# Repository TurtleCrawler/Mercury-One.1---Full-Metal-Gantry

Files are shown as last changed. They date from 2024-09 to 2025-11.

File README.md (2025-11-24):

# Mercury One.1 - Full Metal Gantry

___

 These are a self source design using laser cut aluminum plates from vendors like SendCutSend. The entire belt path and gantry has been moved lower than the stock printed parts. You cannot mix and match these parts with stock printed stepper mounts, xjoints, or front towers. If you already have my metal stepper mounts, you can still use the same metal plates and upgrade to the full metal gantry.

**Assembly steps will be added later, for now you will have to reference the CAD.**
___

**Imperial files:**

- Mainly for those sourcing material in North America
- Files are designed 1/8 inch thick plate (.125in or 3.175mm)

**Metric files:**

- Files are designed for 3mm thick plate (.118in)
- You will also need to use M5 washers under the M5 bolts in the stepper towers to prevent the bolts from bottoming out on the extrusion.

**Other Notes:**

- Top Mount for toolheads designed around the stock Zerog Mercury one.1 belt path.
- Front Mount for any toolhead made for a front mounted MGN12 rail.
- Stepper Tower printed insert pairs should measure slightly less than the height of the aluminum spacers used. If your pairs are 0.2-0.4mm short, you can use the offset files to reduce the gap.
- 9mm Xjoints are designed for a live idler setup, which will require modifying a 20t pulley by removing the hub.
- Youtube Video on pulling the Hub <https://youtu.be/RKpxDKYOJYs?si=vfwZNFjSuAocWLpN>

**Tools Needed:**

- Drill press
- 90 degree Countersinking bit (82 degree also works)
- 220 grit sandpaper (For sanding dowel pins to fit into the bearings)
- Cordless drill (Use with a spare dowel pin to ream the dowel pin holes to size as needed)

___

## 9mm Full Metal Gantry With Live Idler

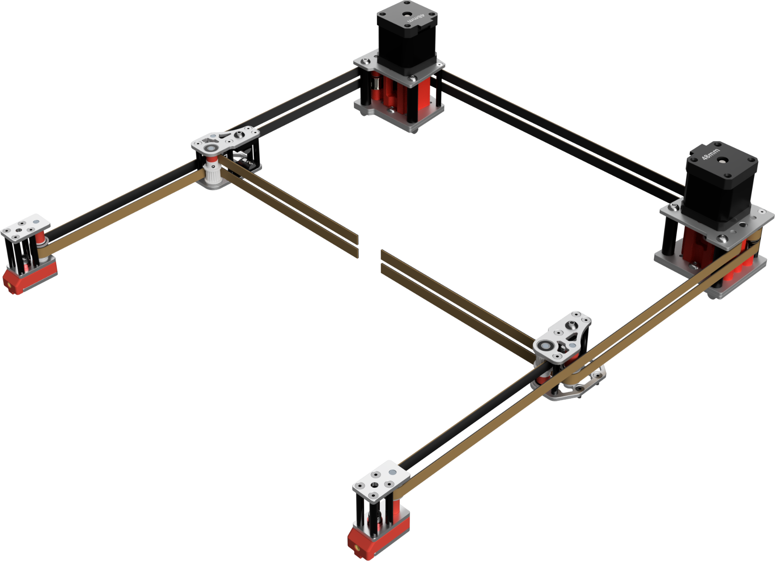
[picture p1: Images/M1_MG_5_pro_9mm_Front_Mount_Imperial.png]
 

___

## 6mm Full Metal Gantry

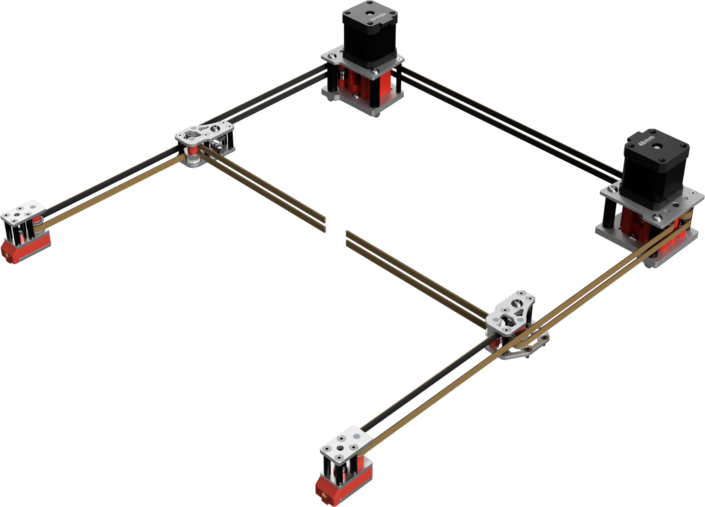
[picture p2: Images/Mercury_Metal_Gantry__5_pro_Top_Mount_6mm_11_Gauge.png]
Metal Stepper Towers
  

___

## Sourcing

Laser cutting services:

- Sendcutsend <https://sendcutsend.com/>
- Laserboost <https://www.laserboost.com/>

Aluminum Spacers and Standoffs:

- D5xM3 Length 10mm <https://www.aliexpress.us/item/3256805776299657.html>
- M5 Length 3mm or 4mm <https://www.aliexpress.us/item/3256802832337103.html>
- 5mmx8mm 35/40mm Spacers <https://www.aliexpress.us/item/3256805365722139.html>
- M3 Threaded spacers <https://www.aliexpress.us/item/2251832625574286.html>
- 5x26mm Dowel Pins <https://www.aliexpress.us/item/3256803593912582.html>
- 5x36mm 5x26mm Dowel Pins <https://www.aliexpress.us/item/2251832864425146.html>
- M5 shims <https://www.aliexpress.us/item/3256801130894631.html>

___

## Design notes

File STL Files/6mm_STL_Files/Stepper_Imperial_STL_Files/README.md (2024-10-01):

# Mercury One.1 - Full Metal Gantry

## 6mm Imperial Stepper Mount Files

These are the files for 6mm belts using Imperial 1/8in thick plates (.125in or 3.175mm) If your plates are 3mm (.118in) then please use the Metric files.

## Offset Files

The offset files have an extra 0.2mm added to the bottom faces. This is due to some printers loosing up to 1 layer height in the start of the prints. First print the standard files, and measure the stack height for the left and right sets. They should add up to 34.81mm to 35mm. If they come in 0.2mm short, you can reprint either the tops or bottoms. And if they are 0.4mm short, then print all of the files needed from the offset files. (A gap of 0.2mm to 0.4mm is also mainly just cosmetic, so you can also skip reprinting if the gap does not bother you.)

## Double Shear Bearing Support Files

5mm shafts without being supported on the other end of the pulley, limit your belt tension to around 110hz. Going past this could bend your stepper shafts. I have included files to support a handful of bearings for a double shear setup. You will need stepper motors with longer stepper shafts than normal, 40 or longer. See the chart bellow for supported bearings.

### Motor and Bearing supports

- Kraken motors (40x5mm Shafts) should work with 625-2RS (5x16x5mm) and 635-RS (5x19x6mm) bearings.
- 55x5mm Shafts will work with 625-RS (5x16x5mm) and 635-2RS (5x19x6mm) bearings.
- 55x8mm Shafts will work with 698-RS (8x19x6mm) and F608-2RS (8x22x7mm) bearings.

### Bearing Notes

- F in front of a bearing name denotes that it is a flanged bearing
- 2RS on the end of a bearing part number means it has 2 Rubber Seals
- RS calls for one rubber seal, and one open side. Though often stores like Amazon will list their 2RS bearings using just RS.
- ZZ on the end of a bearing part number means it uses 2 metal shields in place of seals.
- You will most likely need to sand the ends of your stepper shafts to fit the bearing bores.
- F608-2RS note: I recommend using green bearing retaining compound on the outside fo the bearing, as the 22mm holes in the laser cut plates are not a press fit.

___

Flange stacks are same as the stock Mercury one.1, all shims are M5x1 and placed as shown in the image below.

Stepper Mount Bearing Stacks

Countersink the holes marked in red. Marking them in advanced with a sharpie can help prevent countersinking the wrong holes. You only need to countersink 4 of the 6 plates.

Stepper Mount Countersink Holes

___

## DXF Plate BOM

| Part Description | Quantity |
|---|---|
| Stepper Top-Center Plate_x4.dxf | 4 |
| Stepper Bottom Plate_x2.dxf | 2 |

## 6mm Imperial Stepper Mount Hardware BOM

| Part Description | Quantity |
|---|---|
| M3x30 standoffs | 8 |
| M5x30 Spacer (8 or 10mm OD) | 4 |
| 5x40mm Dowel Pins | 4 |
| *F695RS Bearing | 12 |
| *6mm 20t 5mm Bore GT2 Pulley | 2 |
| M3x10 FHCS | 12 |
| M3x12 FHCS | 12 |
| M5x12 BHCS | 2 |
| M5x50 BHCS | 4 |
| M3x4x5mm Heatsets (5mm OD) | 12 |
| M5x1 Shim | 16 |
| **M5x0.1 Shim | 8 |

*Included in default Mercury One.1 BOM

**Optional parts

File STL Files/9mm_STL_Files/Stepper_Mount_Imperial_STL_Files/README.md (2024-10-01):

# Mercury One.1 - Full Metal Gantry

## 9mm Imperial Stepper Mount Files

These are the files for 9mm belts using Imperial 1/8in thick plates (.125in or 3.175mm) If your plates are 3mm (.118in) then please use the Metric files.

## Offset Files

The offset files have an extra 0.2mm added to the bottom faces. This is due to some printers loosing up to 1 layer height in the start of the prints. First print the standard files, and measure the stack height for the left and right sets. They should add up to 34.81mm to 35mm. If they come in 0.2mm short, you can reprint either the tops or bottoms. And if they are 0.4mm short, then print all of the files needed from the offset files. (A gap of 0.2mm to 0.4mm is also mainly just cosmetic, so you can also skip reprinting if the gap does not bother you.)

## Double Shear Bearing Support Files

5mm shafts without being supported on the other end of the pulley, limit your belt tension to around 110hz. Going past this could bend your stepper shafts. I have included files to support a handful of bearings for a double shear setup. You will need stepper motors with longer stepper shafts than normal, 40 or longer. See the chart bellow for supported bearings.

### Motor and Bearing supports

- Kraken motors (40x5mm Shafts) should work with 625-2RS (5x16x5mm) and 635-RS (5x19x6mm) bearings.
- 55x5mm Shafts will work with 625-RS (5x16x5mm) and 635-2RS (5x19x6mm) bearings.
- 55x8mm Shafts will work with 698-RS (8x19x6mm) and F608-2RS (8x22x7mm) bearings.

### Bearing Notes

- F in front of a bearing name denotes that it is a flanged bearing
- 2RS on the end of a bearing part number means it has 2 Rubber Seals
- RS calls for one rubber seal, and one open side. Though often stores like Amazon will list their 2RS bearings using just RS.
- ZZ on the end of a bearing part number means it uses 2 metal shields in place of seals.
- You will most likely need to sand the ends of your stepper shafts to fit the bearing bores.
- F608-2RS note: I recommend using green bearing retaining compound on the outside fo the bearing, as the 22mm holes in the laser cut plates are not a press fit.

___

Flange stacks Use M5x1 shims, refer to the image below for placement.

Stepper Mount Bearing Stacks

Countersink the holes marked in red. Marking them in advanced with a sharpie can help prevent countersinking the wrong holes. You only need to countersink 4 of the 6 plates.

Stepper Mount Countersink Holes

___

## DXF Plate BOM

| Part Description | Quantity |
|---|---|
| Stepper Top-Center Plate_x4.dxf | 4 |
| Stepper Bottom Plate_x2.dxf | 2 |

## 9mm Imperial Stepper Mount Hardware BOM

| Part Description | Quantity |
|---|---|
| M3x40 standoffs | 8 |
| M5x40 Spacer (8 or 10mm OD) | 4 |
| 5x50mm Dowel Pins | 4 |
| *F695RS Bearing | 12 |
| 695RS Bearing | 6 |
| 9mm 20t 5mm Bore GT2 Pulley | 2 |
| M3x10 FHCS | 12 |
| M3x12 FHCS | 12 |
| M5x12 BHCS | 2 |
| M5x55 BHCS | 4 |
| M3x4x5mm Heatsets (5mm OD) | 12 |
| M5x1 Shim | 10 |
| **M5x0.1 Shim | 8 |

*Included in default Mercury One.1 BOM

**Optional parts

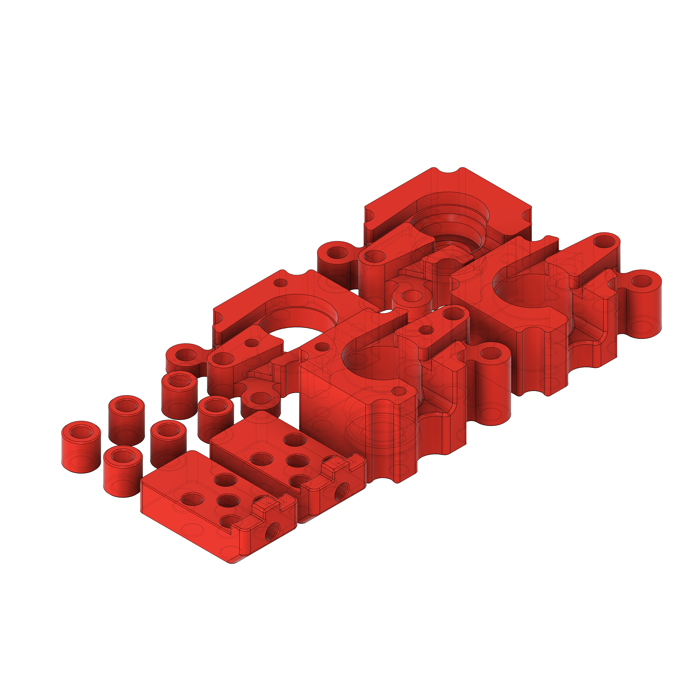
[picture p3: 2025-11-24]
Images/6mm Standard.png

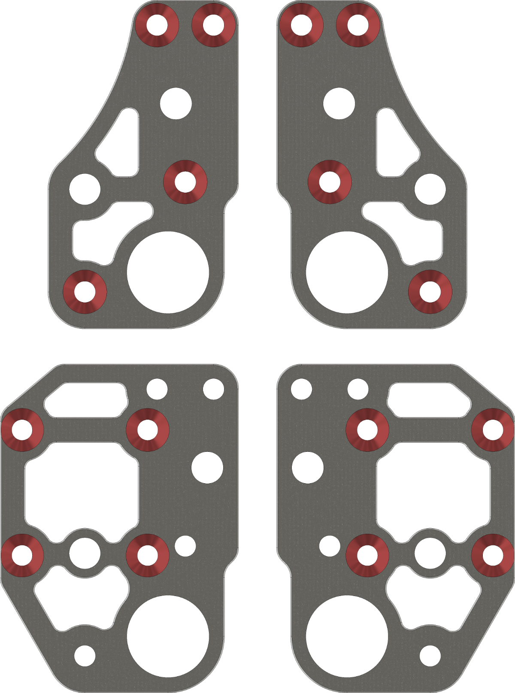
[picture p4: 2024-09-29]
Images/9mm_Xjoint_Countersink_Top.png

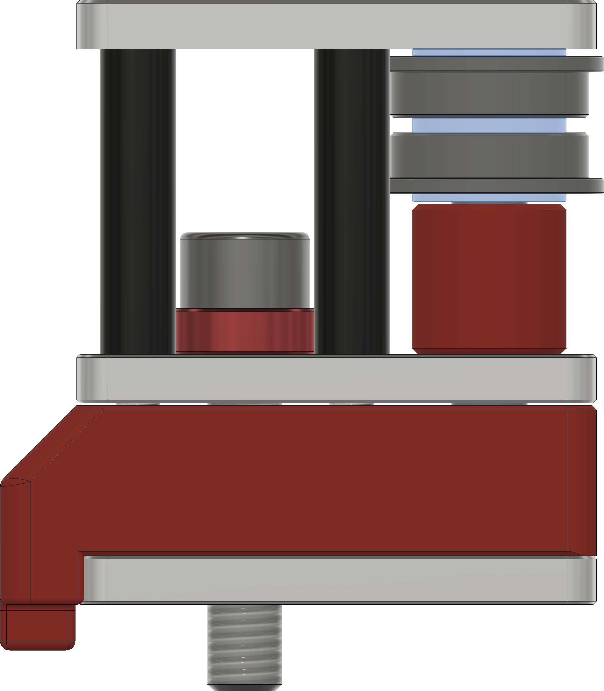
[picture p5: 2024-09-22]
Images/6mm_Front_Tower_Flange_Stack.png

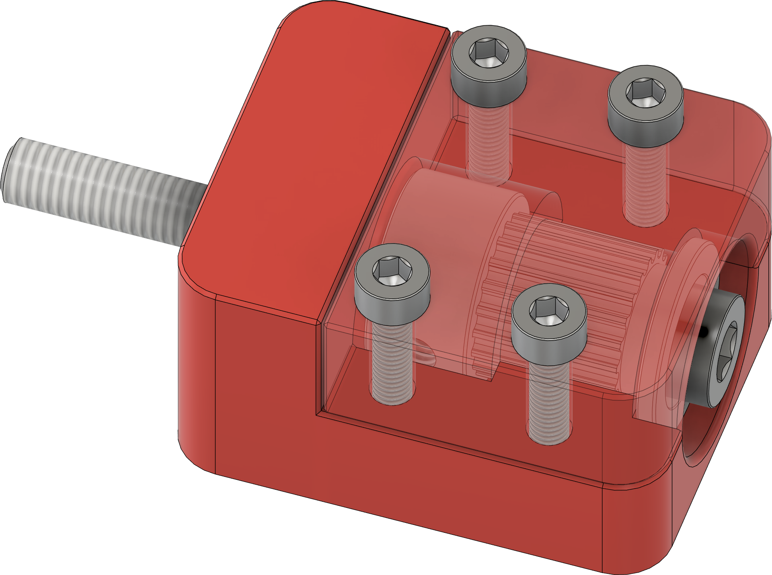
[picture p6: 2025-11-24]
Images/Gates 9mm Pulley - Dehubbing 04.png

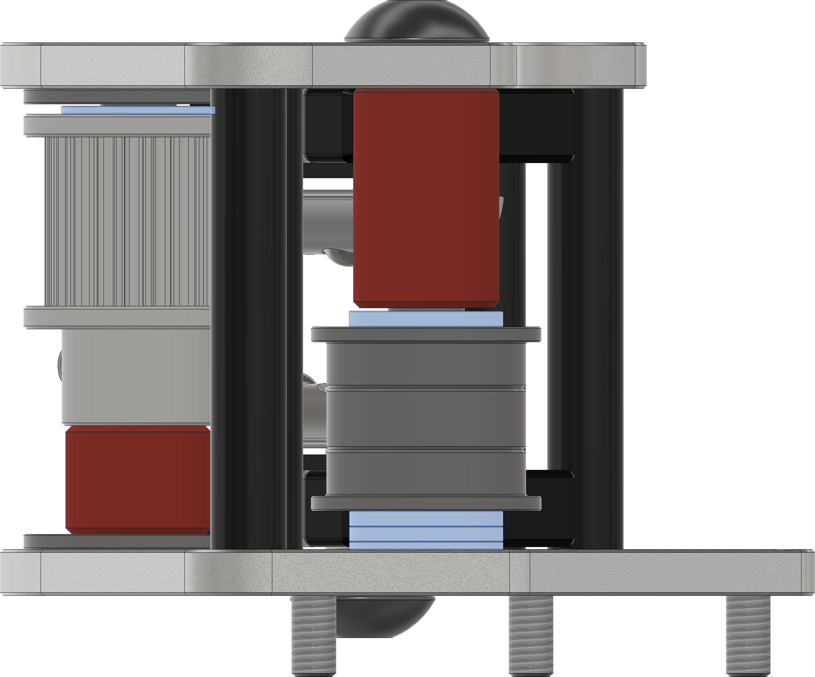
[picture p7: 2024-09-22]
Images/9mm_Metal_Xjoints_Flange_Stack.png

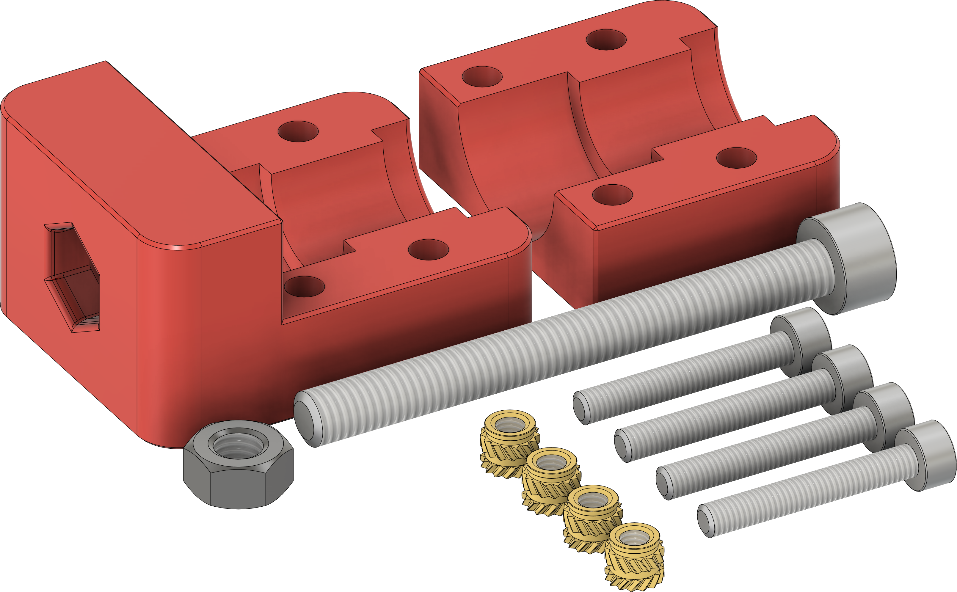
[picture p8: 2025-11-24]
Images/Gates 9mm Pulley - Dehubbing Tool.png

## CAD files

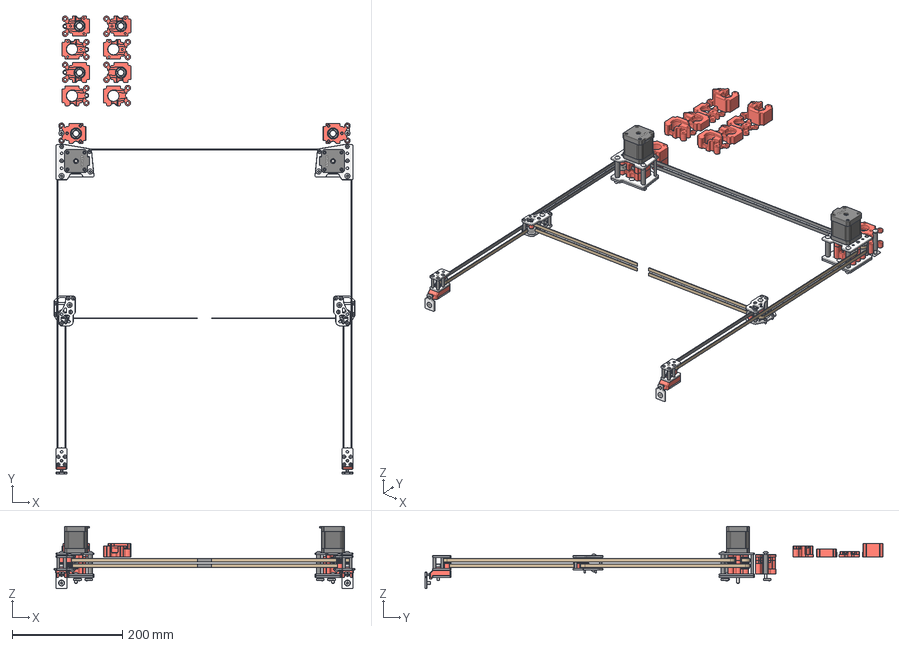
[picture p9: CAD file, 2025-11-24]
CAD_Step_Files/6mm_Front_Mount/FMG_5_Plus_6mm_Front_Mount_Imperial.step
545.0 x 830.2 x 112.5 mm
Belt x 2
Bottom Plate
Top Plate
Center Plate
Printed Heatset Spacer (1)
m3x20mm threaded Standoff x 4
Parallel pin 5 x 30 (1)
5x10x0.5-Shim x 2
F695 2RS (1) x 2
5x10x1-Shim (1) (1)
5x10x3 Aluminum Spacer
Hexagon Socket Countersunk Head Cap Screw DIN 7991 - M3x10 Steel 4.6 Plain v1 x 4
Hexagon Socket Countersunk Head Cap Screw DIN 7991 - M3x20 Steel 4.6 Plain v1 x 4
Hexagon Socket Head Cap Screw DIN 912 - M5 x 0.8 x 25 Steel 4.6 Plain v1
M3 x D5 x L4 Heatset x 7
Spacer
3x5x10 spacers
Bottom Plate (1)
Top Plate (1)
Center Plate (1)
Printed Heatset Spacer (1)(Mirror)
m3x30mm threaded Standoff(Mirror) x 4
Parallel pin 5 x 30
5x10x0.5-Shim (1) x 2
F695 2RS x 2
5x10x1-Shim
Hexagon Socket Countersunk Head Cap Screw DIN 7991 - M3x10 Steel 4.6 Plain v1(Mirror) x 4
Hexagon Socket Countersunk Head Cap Screw DIN 7991 - M3x20 Steel 4.6 Plain v1(Mirror) x 4
Hexagon Socket Head Cap Screw DIN 912 - M5 x 0.8 x 20 Steel 4.6 Plain v2(Mirror)
M3 x D5 x L4 Heatset(Mirror)
Spacer(Mirror)
5x10x3 Aluminum Spacer(Mirror)
3x5x10 spacers(Mirror)
Bottom Plate_1
Center Plate_1
Top Plate_1
M3x35 Standoff x 3
M5 Spacer x 3
Printed_Top_Left_Insert x 2
Printed_Top_Left_Insert_M5_Mod x 2
Printed_Bottom_Left_Insert_M5_Mod x 2
Printed_Bottom_Left_Insert x 2
SHIM x 3
F695 Bearing x 2
SHIM (1) x 5
F695 Bearing (1) x 4
Nema 17 48mm <1> x 2
20t 2gt Pulley 5mm x 2
Hex socket set screw with cone point M4x0.7 x 4 x 4
Pin 5 x 30 x 2
M3 x D5 x L4 Heatset(Mirror)_1 x 6
Printed_Top_Right_Insert x 2
Printed_Top_Right_Insert_M5_Mod x 2
M5 Spacer(Mirror) x 3
Printed_Bottom_Right_Insert x 2
Printed_Bottom_Right_Insert_M5_Mod x 2
SHIM (1)(Mirror) x 5
F695 Bearing (1)(Mirror) x 4
SHIM(Mirror) x 3
F695 Bearing(Mirror) x 2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

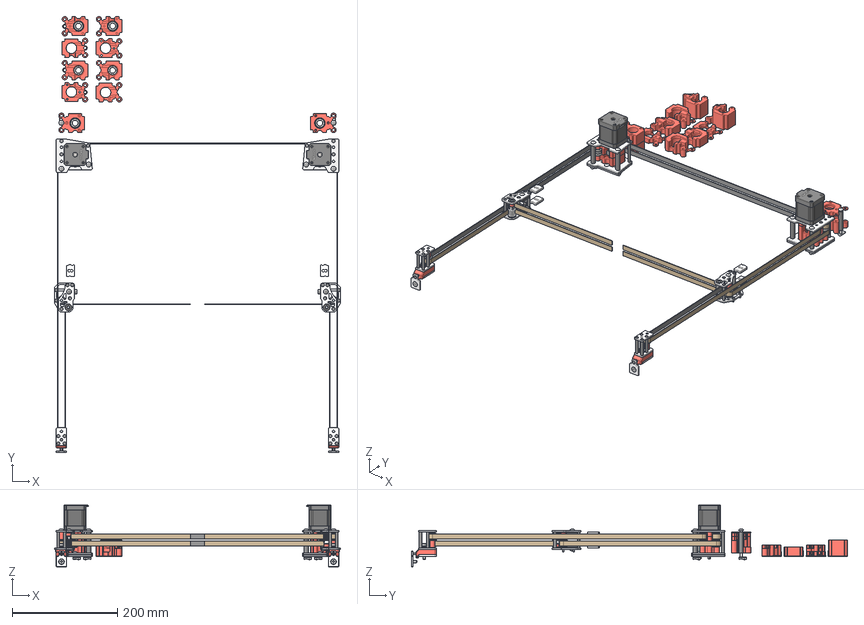
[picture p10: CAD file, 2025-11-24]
CAD_Step_Files/9mm_Front_Mount/FMG_5_Plus_9mm_Front_Mount_Imperial.step
545.0 x 830.1 x 117.5 mm
Belt x 2
m3x30mm threaded Standoff x 4
Left Bottom
Left Top
DIN 7991 - M3x8 Steel 4.6 Plain x 12
Parallel pin 5 x 30 (1)
5x10x1-Shim (1) x 3
F695 2RS (1) x 4
F695 2RS (1) (1)
5x10x1-Shim (1) (1) x 2
DXF Exports
Parallel pin 5 x 30 (1) (1)
DIN 913 - M4 x 4 Steel 4.6 Plain x 2
9mm Xjoint Tall Spacer
9mm Live Idler Spacer
2020 Spacers
Metal_Gantry_Spacer x 2
Metal_Gantry_Spacer(Mirror) x 2
M5 Roll In T-Nut x 10
Hexagon Socket Button Head Screw ISO 7380-1 - M5 x 12 Steel 4.6 Plain v2 x 2
Left Bottom(Mirror)
Left Top(Mirror)
m3x30mm threaded Standoff(Mirror) x 4
Hexagon Socket Countersunk Head Cap Screw DIN 7991 - M3x8 Steel 4.6 P lain v1(Mirror) x 12
Parallel pin 5 x 30 (1)(Mirror)
5x10x1-Shim (1)(Mirror) x 3
F695 2RS (1)(Mirror) x 4
F695 2RS (1) (1)(Mirror)
5x10x1-Shim (1) (1)(Mirror) x 2
DXF Exports(Mirror)
Parallel pin 5 x 30 (1) (1)(Mirror)
Set Screw DIN 913 - M3 x 3 Steel 4.6 Plain v1(Mirror) x 2
Component53(Mirror)
Component54(Mirror)
2020 Spacers(Mirror)
M5 Roll In T-Nut v1(Mirror) x 2
Hexagon Socket Button Head Screw ISO 7380-1 - M5 x 12 Steel 4.6 Plain v2(Mirror) x 2
Metal_Gantry_Spacer(Mirror) (1) x 2
Metal_Gantry_Spacer(Mirror)(Mirror) x 2
Bottom Plate
Top Plate
Center Plate
Printed Heatset Spacer
Parallel pin 5 x 40
5x10x1-Shim (1)_1 x 3
F695 2RS (1)_1 x 2
F695 2RS (1) (1)_1
5x10x0.5-Shim x 2
m3x30mm threaded Standoff_1 x 4
5x10 Aluminum Spacer
Hexagon Socket Countersunk Head Cap Screw DIN 7991 - M3x10 Steel 4.6 Plain v1 x 4
Hexagon Socket Countersunk Head Cap Screw DIN 7991 - M3x20 Steel 4.6 Plain v1 x 4
Hexagon Socket Head Cap Screw DIN 912 - M5 x 0.8 x 25 Steel 4.6 Plain v1
3x5x10 spacers
Printed Flangestack Spacer
M3 x D5 x L4 Heatset x 7
Bottom Plate (1)
Top Plate (1)
Center Plate (1)
Printed Heatset Spacer(Mirror)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

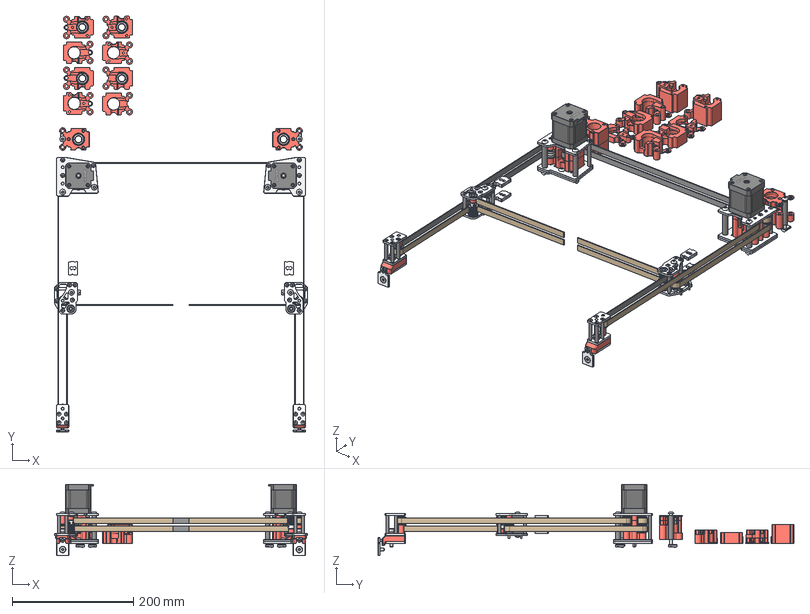
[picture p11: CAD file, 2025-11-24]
CAD_Step_Files/9mm_Top_Mount/FMG_5_pro_9mm_Top_Mount_Imperial.step
417.0 x 685.1 x 117.5 mm
Belt x 2
m3x30mm threaded Standoff x 4
Left Bottom
Left Top
DIN 7991 - M3x8 Steel 4.6 Plain x 12
Parallel pin 5 x 30 (1)
5x10x1-Shim (1) x 3
F695 2RS (1) x 4
F695 2RS (1) (1)
5x10x1-Shim (1) (1) x 2
DXF Exports
Parallel pin 5 x 30 (1) (1)
DIN 913 - M4 x 4 Steel 4.6 Plain x 2
9mm Xjoint Tall Spacer
9mm Live Idler Spacer
2020 Spacers
Metal_Gantry_Spacer x 2
Metal_Gantry_Spacer(Mirror) x 2
M5 Roll In T-Nut x 10
Hexagon Socket Button Head Screw ISO 7380-1 - M5 x 12 Steel 4.6 Plain v2 x 2
Left Bottom(Mirror)
Left Top(Mirror)
m3x30mm threaded Standoff(Mirror) x 4
Hexagon Socket Countersunk Head Cap Screw DIN 7991 - M3x8 Steel 4.6 P lain v1(Mirror) x 12
Parallel pin 5 x 30 (1)(Mirror)
5x10x1-Shim (1)(Mirror) x 3
F695 2RS (1)(Mirror) x 4
F695 2RS (1) (1)(Mirror)
5x10x1-Shim (1) (1)(Mirror) x 2
DXF Exports(Mirror)
Parallel pin 5 x 30 (1) (1)(Mirror)
Set Screw DIN 913 - M3 x 3 Steel 4.6 Plain v1(Mirror) x 2
Component53(Mirror)
Component54(Mirror)
2020 Spacers(Mirror)
M5 Roll In T-Nut v1(Mirror) x 2
Hexagon Socket Button Head Screw ISO 7380-1 - M5 x 12 Steel 4.6 Plain v2(Mirror) x 2
Metal_Gantry_Spacer(Mirror) (1) x 2
Metal_Gantry_Spacer(Mirror)(Mirror) x 2
Bottom Plate
Top Plate
Center Plate
Printed Heatset Spacer
Parallel pin 5 x 40
5x10x1-Shim (1)_1 x 3
F695 2RS (1)_1 x 2
F695 2RS (1) (1)_1
5x10x0.5-Shim x 2
m3x30mm threaded Standoff_1 x 4
5x10 Aluminum Spacer
Hexagon Socket Countersunk Head Cap Screw DIN 7991 - M3x10 Steel 4.6 Plain v1 x 4
Hexagon Socket Countersunk Head Cap Screw DIN 7991 - M3x20 Steel 4.6 Plain v1 x 4
Hexagon Socket Head Cap Screw DIN 912 - M5 x 0.8 x 25 Steel 4.6 Plain v1
3x5x10 spacers
Printed Flangestack Spacer
M3 x D5 x L4 Heatset x 7
Bottom Plate (1)
Top Plate (1)
Center Plate (1)
Printed Heatset Spacer(Mirror)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

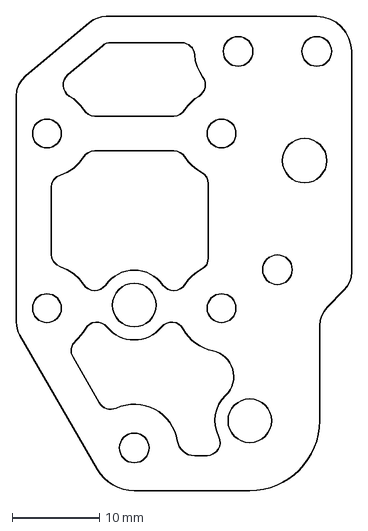
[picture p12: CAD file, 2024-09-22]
DXF_Files/6mm_Front_Mount_Xjoints/FMG_6mm_Front_Mount_Xjoint_Bottom_x2.dxf
38.4 x 54.3 mm

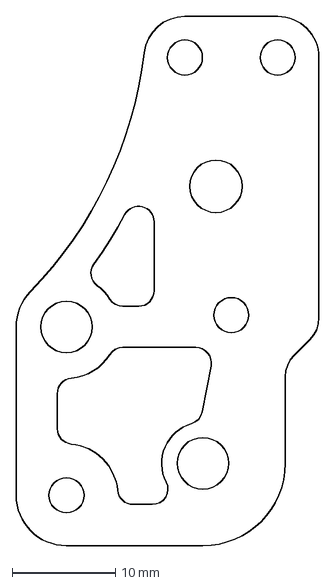
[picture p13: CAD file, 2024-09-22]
DXF_Files/6mm_Top_Mount_Xjoints/FMG_6mm_Top_Mount_Xjoint_Top_x2.dxf
29.4 x 51.4 mm

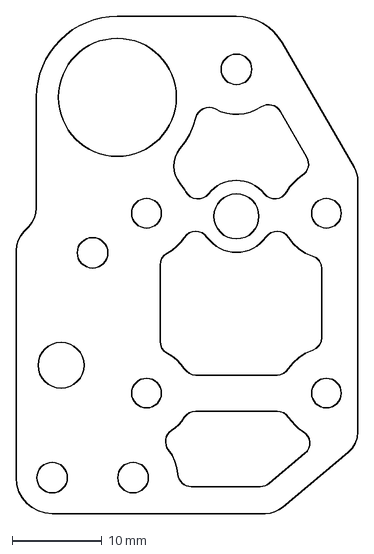
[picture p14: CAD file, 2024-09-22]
DXF_Files/9mm_Front_Mount_Xjoints/FMG_9mm_Front_Mount_Xjoint_Bottom_x2.dxf
38.0 x 55.3 mm

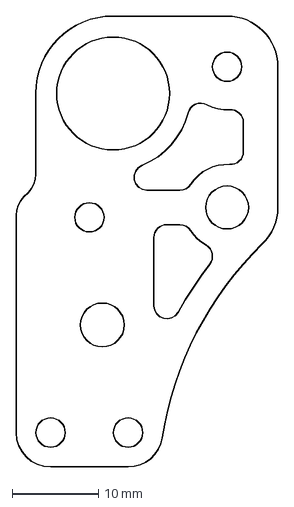
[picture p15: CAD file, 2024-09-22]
DXF_Files/9mm_Top_Mount_Xjoints/FMG_9mm_Top_Mount_Xjoint_Top_x2.dxf
30.4 x 52.4 mm

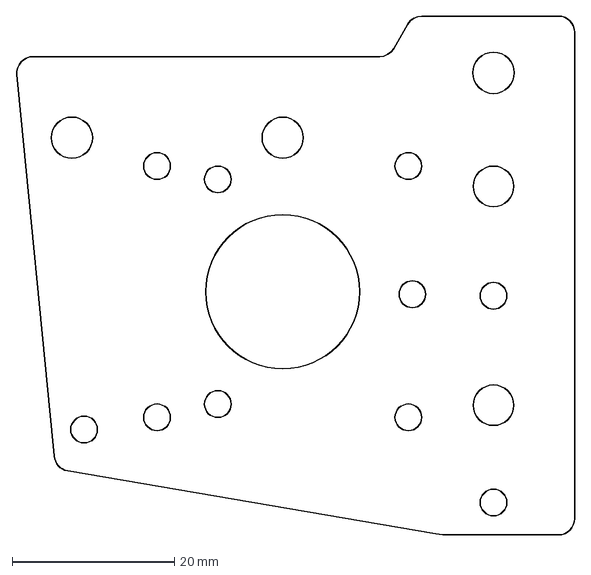
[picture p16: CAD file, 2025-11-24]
DXF_Files/FMG_StepperTower_Center_Plate.dxf
68.8 x 64.0 mm

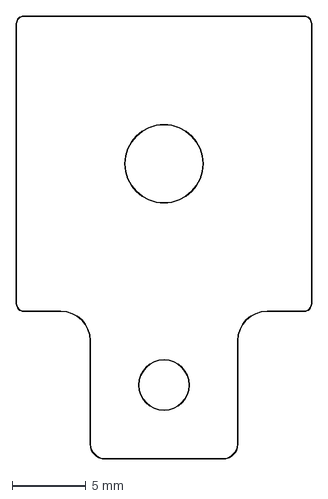
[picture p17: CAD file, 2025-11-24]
DXF_Files/Optional/FMG_FrontTensionPlate.dxf
20.0 x 30.0 mm

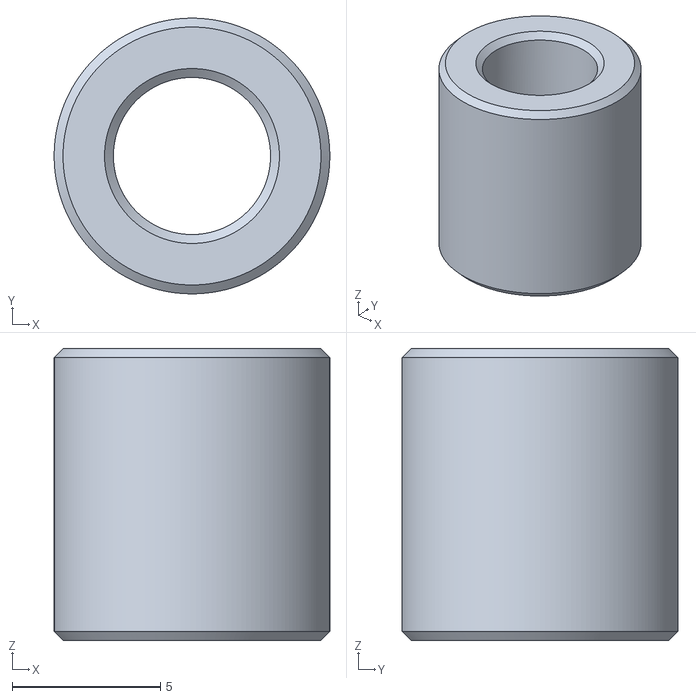
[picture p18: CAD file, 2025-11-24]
STL Files/6mm_STL_Files/6mm_Flange_Stack_Spacer_x4.stl
9.30 x 9.30 x 9.85

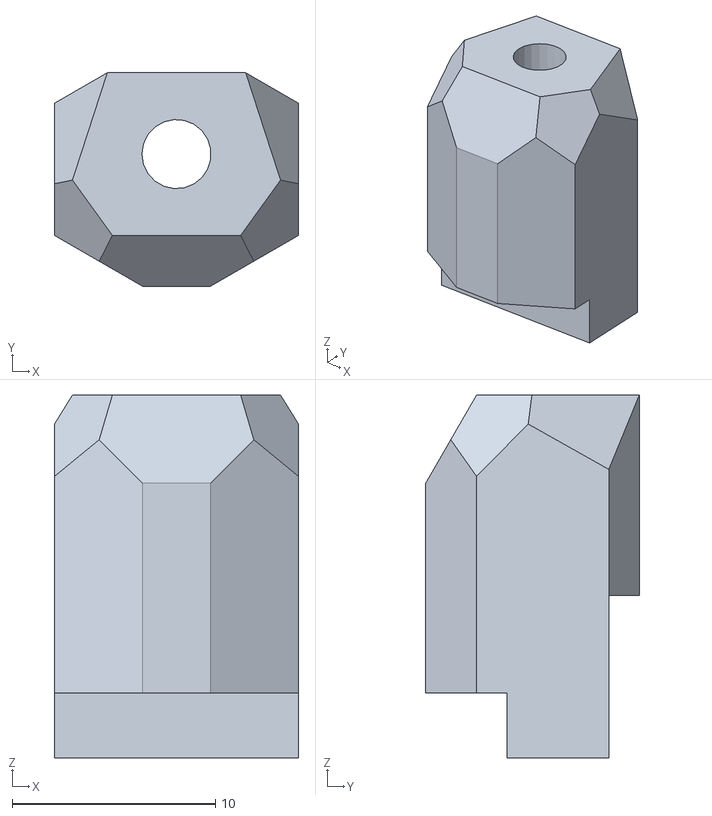
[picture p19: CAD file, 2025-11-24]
STL Files/6mm_STL_Files/Other/5Pro_X_Endstop_Metal_Gantry.stl
12.0 x 10.5 x 17.9

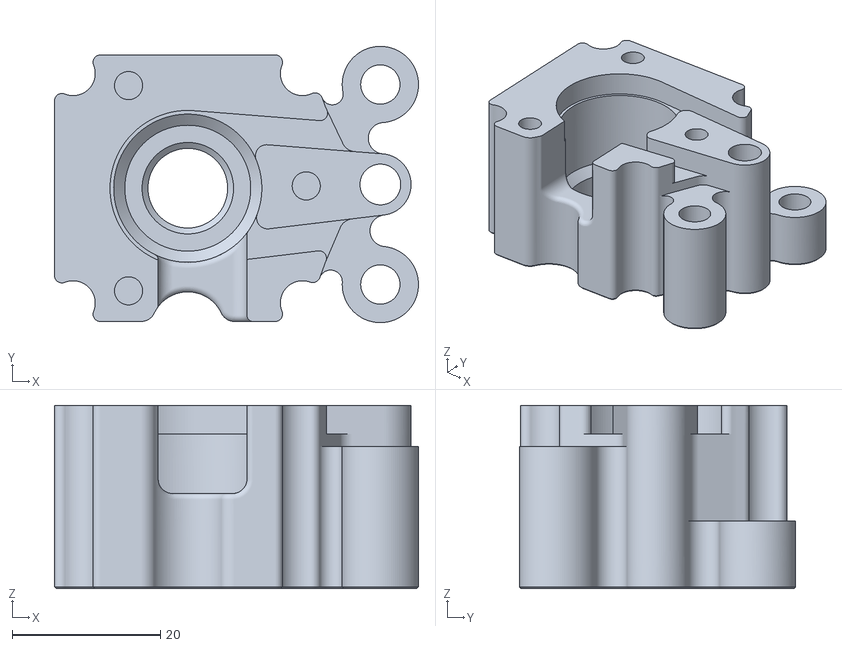
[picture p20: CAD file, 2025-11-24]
STL Files/6mm_STL_Files/Stepper_Imperial_STL_Files/6mm_Imperial-Bottom_Right__Insert.stl
49.2 x 37.3 x 24.8

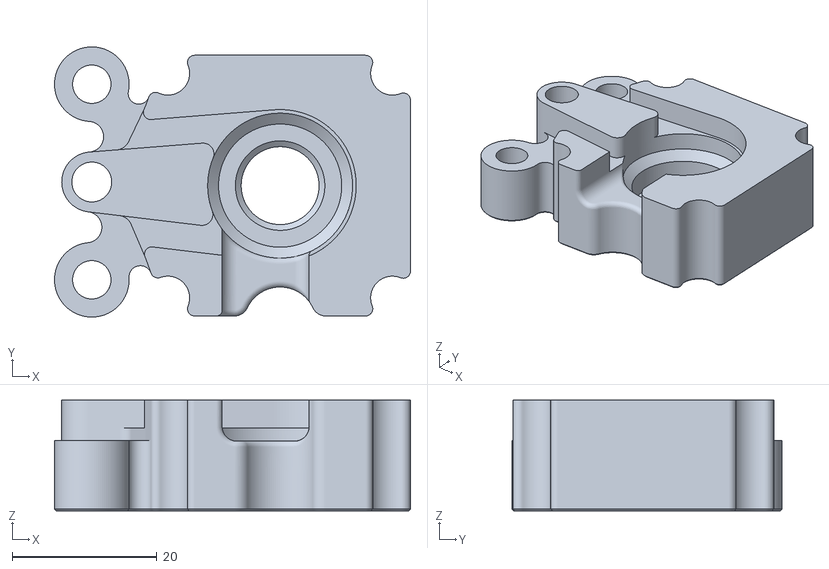
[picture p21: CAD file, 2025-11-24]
STL Files/6mm_STL_Files/Stepper_Metric_STL_Files/Offset/6mm_Metric-Bottom_Left__Insert-Offset.stl
49.1 x 37.3 x 15.3

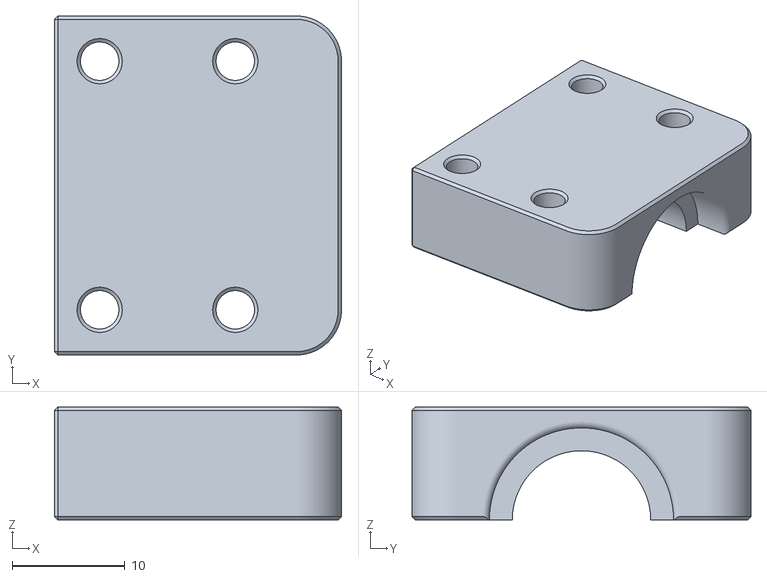
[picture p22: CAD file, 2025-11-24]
STL Files/9mm_STL_Files/Hub_Pulley_Top.stl
25.4 x 30.0 x 10.0

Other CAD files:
CAD_Step_Files/6mm_Top_Mount/FMG_5_Plus_6mm_Top_Mount_Metric.step
STL Files/9mm_STL_Files/Stepper_Mount_Imperial_STL_Files/9mm_Imperial-Top_Left__Insert.stl
STL Files/9mm_STL_Files/Stepper_Mount_Metric_STL_Files/9mm_Metric-Bottom_Left__Insert.stl
STL Files/9mm_STL_Files/Stepper_Mount_Metric_STL_Files/Offset/9mm_Metric-Top_Left__Insert-Offset.stl
CAD_Step_Files/6mm_Front_Mount/FMG_5_Plus_6mm_Front_Mount_Metric.step
CAD_Step_Files/6mm_Front_Mount/FMG_5_pro_6mm_Front_Mount_Imperial.step
CAD_Step_Files/6mm_Front_Mount/FMG_5_pro_6mm_Front_Mount_Metric.step
CAD_Step_Files/6mm_Top_Mount/FMG_5_Plus_6mm_Top_Mount_Imperial.step
CAD_Step_Files/6mm_Top_Mount/FMG_5_pro_6mm_Top_Mount_Imperial.step
CAD_Step_Files/6mm_Top_Mount/FMG_5_pro_6mm_Top_Mount_Metric.step
CAD_Step_Files/9mm_Front_Mount/FMG_5_Plus_9mm_Front_Mount_Metric.step
CAD_Step_Files/9mm_Front_Mount/FMG_5_pro_9mm_Front_Mount_Imperial.step
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

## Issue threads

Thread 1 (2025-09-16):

Front Idler Tower - Connector to

jeremysells, 2025-09-16:
Hey, first off, nice project!

Do you have any details about what the Front Idler Towers connect to?
Specifically, I'm trying to figure out what the front heat insert attaches to.

I've checked the CAD models but couldn't find anything definitive. From some online searching, I found the image below, but it might be from a different project:

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

Thanks in advance!

jeremysells, 2025-09-26:
Thanks @warpedscale !

Closed 2025-09-26.

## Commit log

2024-09-22 Initial Release
    [6mm Front Tower Spacer_x2.stl, 6mm Imperial - Offset - Printed Bottom Right Insert.stl, 6mm Imperial - Offset - Printed Top Left Insert.stl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]
2024-09-22 Copy paste error
    Fixed the Xjoint flange notes, had copied the 9mm notes and forgot to update some sections.
2024-09-22 Added missing 6mm DXF Files
    Added 6mm Xjoint DXF Files.
    [6mm Metal Front Mount Xjoint Bottom_x2.dxf, 6mm Metal Front Mount Xjoint Top_x2.dxf, 6mm Metal Top Mount Xjoint Bottom_x2.dxf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]
2024-09-22 Updated BOM
    Added M3x5x10 spacers to the BOM
2024-09-22 Updated some copy paste errors in the 6mm readme file
2024-09-22 BOM Typo Fix
    Forgot the M5 in front of the M5x0.1mm shims
2024-09-23 Added optional Dowel Pin Sizes
2024-09-29 Added Double Shear Bearing Support
    Fixed STL print file Orientation
    Added more readme files
    Fixed some errors in the step file assemblies
    *Added more typos and copy paste errors
    [6mm Imperial - Bottom Left Insert-625.stl, 6mm Imperial - Bottom Left Insert-635-698.stl, 6mm Imperial - Bottom Left Insert-F608.stl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]
2025-11-24 Updated Bearing Specs and Docs
    New stepper tower plates and inserts.
    [5Pro_X_Endstop_Metal_Gantry.stl, 6mm Front Tower Spacer_x2.stl, 6mm Imperial - Bottom Left Insert-625.stl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]
